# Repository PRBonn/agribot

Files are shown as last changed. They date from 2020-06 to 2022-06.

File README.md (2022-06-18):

## Update
1) remove tf dependencies and included tf2 similar to costmap2D and ros nav core packages. 
2) makes on Melodic and further

# AgriBot - Agricultural Mobile Robot Platform

---

### Youtube video

<div align="center">
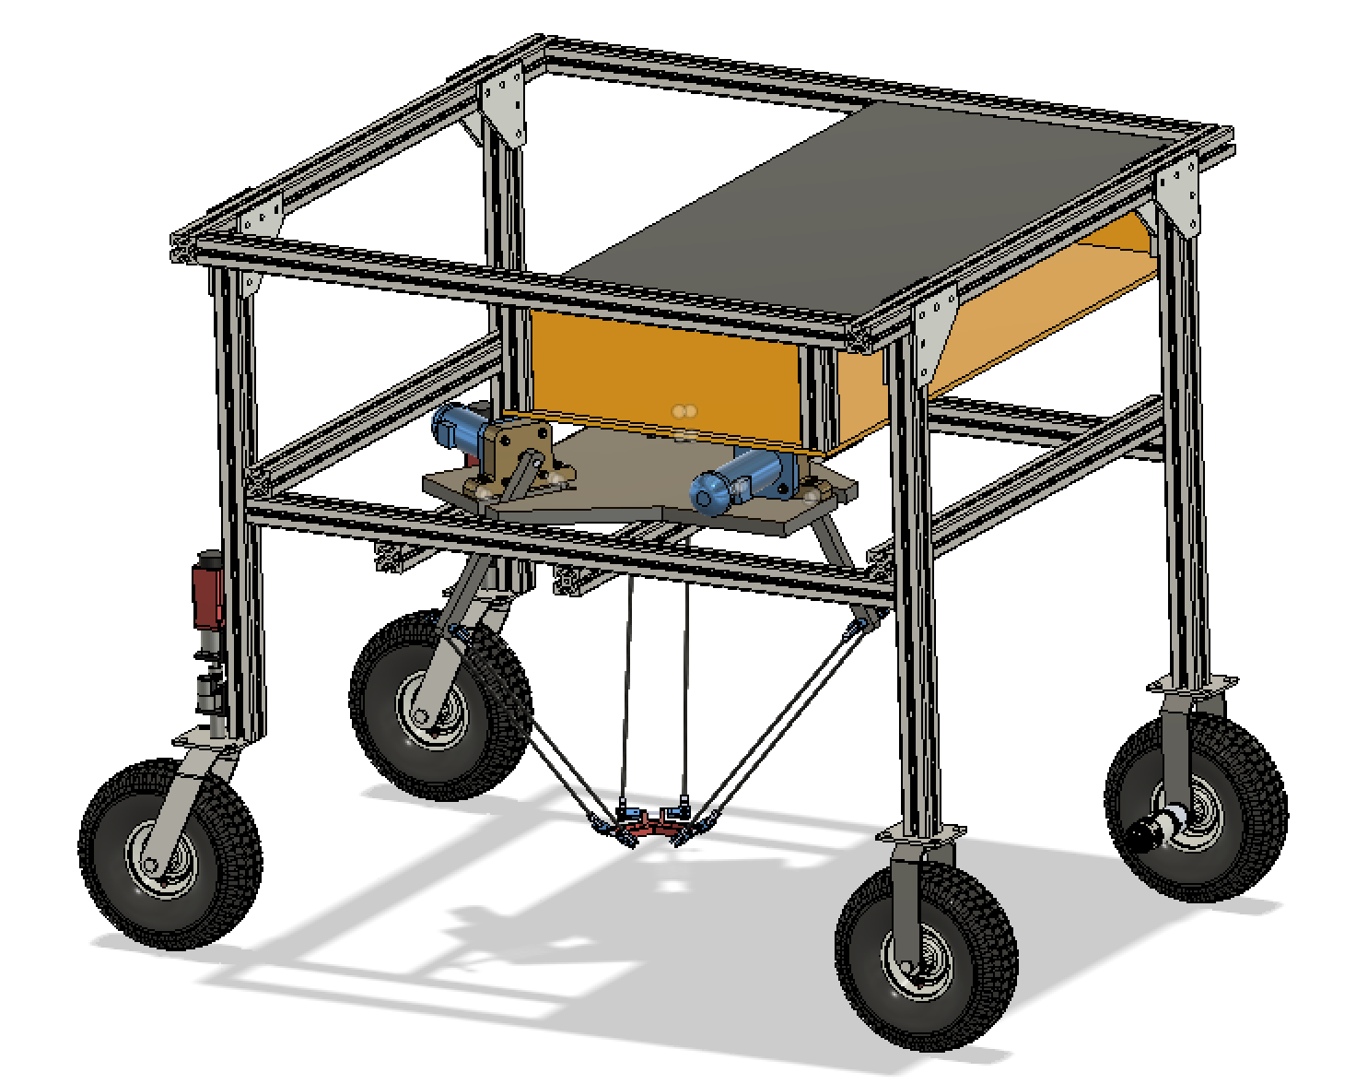
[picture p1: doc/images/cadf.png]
cadf
	
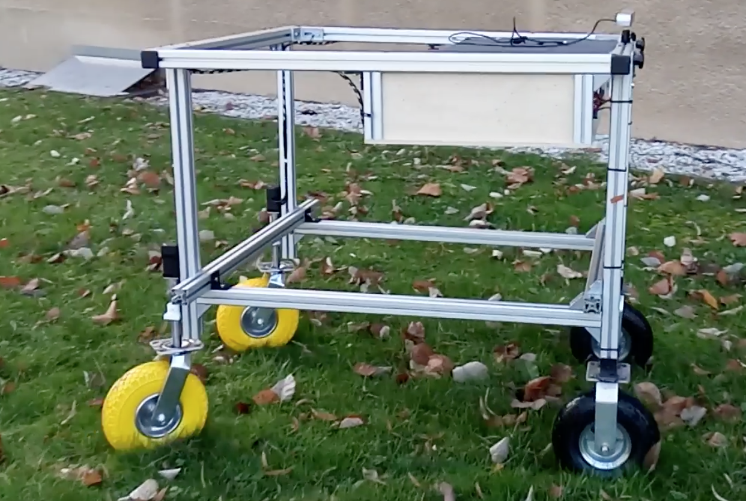
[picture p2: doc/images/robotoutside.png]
robotoutside
	
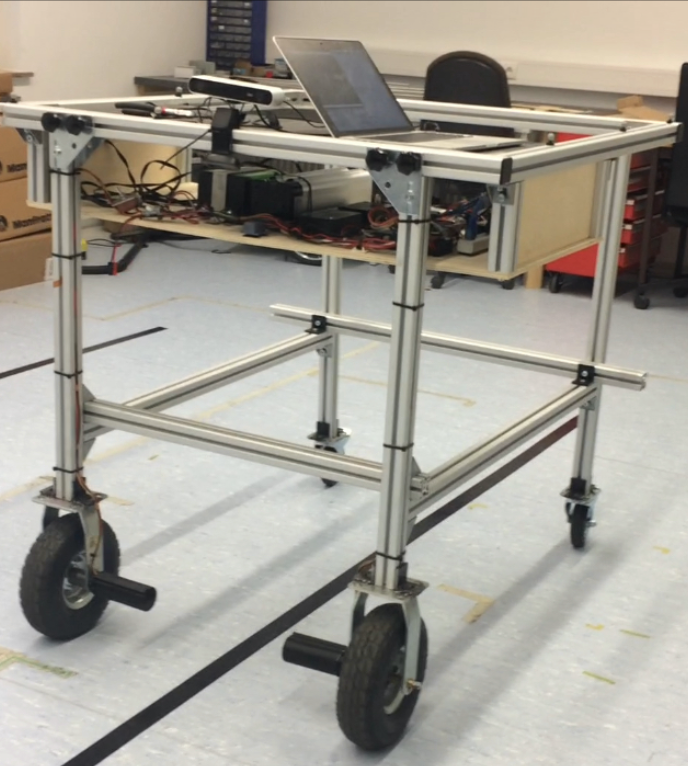
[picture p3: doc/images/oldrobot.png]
oldrobot
	
</div>

---
<div align="center">
	
YouTube Demo (https://youtu.be/aT82Srq7nwY?t=2)
	
</div>

## Project mission

The mission of the project is to build an agricultural robot (AgriBot) from
scratch with the aim of serving as a data-recording platform in fields.
For further information about the design and purpose of the robot, please follow the [About the AgriBot Project page](https://github.com/PRBonn/agribot/blob/master/doc/about.md)

---

## Getting Started
For easily bringing up the robot and recording data refer to [Easy bring up & Record Data](https://github.com/PRBonn/agribot/blob/master/doc/recorddata.md) which provides step-by-step
instructions to run the robot.

---

## Main Sections
- [Easy Bring up & Record Data :](https://github.com/PRBonn/agribot/blob/master/doc/recorddata.md)
  	Instructions for running the robot and recording the sensor data to a bagfile.
- [AgriBot Software :](https://github.com/PRBonn/agribot/blob/master/doc/api.md)
	Details about different packages written for the platform like navigation, localization, base controller, etc.
- [Mechanical Design :](https://github.com/PRBonn/agribot/blob/master/doc/mec.md)
	Detail about how mechanical structure has been designed and improved during the project time.
- [Electrical  Design :](https://github.com/PRBonn/agribot/blob/master/doc/elec.md)
	Electrical schematics and descriptions about connections and wiring protocols used in the robot.
- [Debug:](https://github.com/PRBonn/agribot/blob/master/doc/debug.md)
	Debug procedures for common problems.

---

<div align="center">
  


</div>

---

---
## Citation 
if you use this project in your recent works please reference to our paper by:

```bash

@article{ahmadi2021towards,
  title={Towards Autonomous Crop-Agnostic Visual Navigation in Arable Fields},
  author={Ahmadi, Alireza and Halstead, Michael and McCool, Chris},
  journal={arXiv preprint arXiv:2109.11936},
  year={2021}
}

@inproceedings{ahmadi2020visual,
  title={Visual servoing-based navigation for monitoring row-crop fields},
  author={Ahmadi, Alireza and Nardi, Lorenzo and Chebrolu, Nived and Stachniss, Cyrill},
  booktitle={2020 IEEE International Conference on Robotics and Automation (ICRA)},
  pages={4920--4926},
  year={2020},
  organization={IEEE}
}
```
---

## Maintenance
This repository is maintained by [Alireza Ahmadi](https://github.com/alirezaahmadi). In case of any problems, please don't hesitate to contact me.

 Alireza.Ahmadi@uni-bonn.de

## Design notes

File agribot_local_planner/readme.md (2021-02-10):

# AGRIBOT LOCAL PLANNER #

This package provide a simple implementation of a PID controller for robot
navigation. During robot navigation along a given path, this controller attempts
to stabilize both the linear and rotational velocity in an independent manner.
No velocity profile is computed before the robot starts moving. The environment
is considered static and, at the moment, no dynamics are taken into account.
This has been implemented as a ROS `move_base/base_local_planner` plugin.

## How to build ##

To build this package, just move it to your `catkin_ws` and build.

## How to run ##

The use of this package is constrained to the use of ROS `move_base` framework
for navigation. To use it as `base_local_planner`, add in your launcher in the
tag defining the `move_base` node the following line.
```
<param name="base_local_planner" value="agribot_local_planner/AgribotLocalPlanner" />
```
A simple tuning of the PID controller is provided. However, it may need to be
newly tuned accordingly to the robot and task taken into account. To this end,
controller parameters have been defined as dynamic parameters and can be tuned
using `dynamic_reconfigure`.

Enjoy!

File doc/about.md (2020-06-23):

# AgriBot - A New Agricultural Mobile Robot Platform

---

## About The Project
The aim of the project is to develop a robot to perform basic localization and navigation tasks in agricultural applications. More precisely, the robot should embody a platform that is able to navigate autonomously in the fields and offers enough room for the assembly of task specific actuators like herbicide nozzles or additional sensors like cameras.
To achieve this goal, three main tasks have to be solved: the hardware design, the localization and the navigation. The first stage of development is the mechanical design of the robot. Requirements for the design are, that the platform is lightweight and easy to transport while being big enough to pass over crop rows and having space for the mentioned additional equipment. On top of the design of the layout of the platform, the sensors and actuators used for localization and navigation have to be decided on. The result of this first stage is a platform that can drive while being steered by a joystick controller.
The second step during the development is the localization of the robot. To be able to navigate autonomously it is essential that the robot pose relative to the field is known. Task of the localization is to use the given sensor data and give an estimation of this pose that is precise enough for the last step, the navigation.
During the navigation, the pose estimate of the localization in combination with a map of the field is taken as input and the necessary motion commands to follow a given trajectory through the field are returned. Consequently, at this point in time the joystick controller is not needed any more, as the motion commands are generated by the navigation module and the robot drives autonomously.

<!-- <div align="center">
	<img src="/doc/images/mechanic.png" alt="mechanic" width="600" title="mechanic"/>
</div> -->

---

*Note that* this repository is maintaining by [Alireza Ahamdi](https://github.com/PRBonn). 
In case of facing any problem don't hesitate to constant me.

---
[The Main ReadMe](https://github.com/PRBonn/agribot/blob/master/README.md)

*Section* 
- [Mechanical Design](https://github.com/PRBonn/agribot/blob/master/doc/mec.md)
- [Electrical  Design](https://github.com/PRBonn/agribot/blob/master/doc/elec.md)
- [AgriBot Software](https://github.com/PRBonn/agribot/blob/master/doc/api.md) 
- [Record Data](https://github.com/PRBonn/agribot/blob/master/doc/recorddata.md) 
- [Debug](https://github.com/PRBonn/agribot/blob/master/doc/debug.md)

--- 
  by: [Alireza Ahmadi](https://github.com/alirezaahmadi)                                     
 University of Bonn- Robotics & Geodetic Engineering

 Alireza.Ahmadi@uni-bonn.de

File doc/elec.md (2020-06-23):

# AgriBot - A New Agricultural Mobile Robot Platform

---

**`WARNING`** please attention to warnings:
- In case of having some pins disconnected or broken, please first read the tutorials to debug the problem and **'do not try your luck, otherwise, definitely you will burn some part!!!'**, or you can contact with [Alireza Ahmadi](https://github.com/PRBonn) as the designer of the robot.
- In case of noticing any delay in responds from the robot, please restart the nodes and connections.
- Always check the main connections (power, USB cables, Joystick) before turning the robot 'ON'.

---

## Table of Contents
- [Electrical Design](https://github.com/PRBonn/agribot/blob/master/doc/elec.md#electrical-design)
  - [Power UP the AgriBot](https://github.com/PRBonn/agribot/blob/master/doc/elec.md#power-up-the-agribot)
  	- [Logic level Battery](https://github.com/PRBonn/agribot/blob/master/doc/elec.md#logic-level-battery)
  	- [High level Battery](https://github.com/PRBonn/agribot/blob/master/doc/elec.md#high-level-battery)
    - [How to Charge the Agribot](https://github.com/PRBonn/agribot/blob/master/doc/elec.md#how-to-charge-the-agribot)
  - [Power Management Part](https://github.com/PRBonn/agribot/blob/master/doc/elec.md#power-management-part)
  - [Serial Communication, I/O Pins](https://github.com/PRBonn/agribot/blob/master/doc/elec.md#serial-communication-io-pins)
  	- [IMU node Connection](https://github.com/PRBonn/agribot/blob/master/doc/elec.md#imu-connection)
  	- [RearServo's Connections](https://github.com/PRBonn/agribot/blob/master/doc/elec.md#rearservos-connections)
  	- [Front Actuators Connections](https://github.com/PRBonn/agribot/blob/master/doc/elec.md#front-actuators)
  - [Reset Relays](https://github.com/PRBonn/agribot/blob/master/doc/elec.md#reset-relays)
  - [Alarm](https://github.com/PRBonn/agribot/blob/master/doc/elec.md#alarms)

---

## Electrical Design

Electrical section of the AgriBot includes controlling layers, sensors, battery management system (BMS) and actuators. The control layers’ structure is shown in below which is comprised of two different major layers, Low-level controllers and User layer which are containing DCM (Device Communication Manager), Sensors and User layers. The main program executed on Low-level controller runs on a Raspberry Pi 3 embedded controller and directly controls all the sensors and actuators, also runs master of ROS to manage all nodes working in the network. This layer is responsible for time synchronization of whole connections and I/O’s used in the process, like reading the IMU (Inertial Measurement Unit) and controlling all four actuators for driving and steering the robot. 

<div align="center">
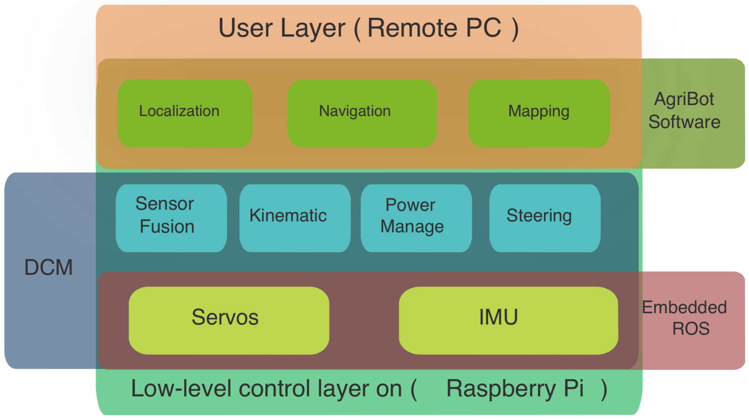
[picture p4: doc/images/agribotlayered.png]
agribotlayered
  
</div>

Also, it runs the main nodes which drive the robot based on defined kinematics and provides a basic fusion of the sensors for localization out of IMU, wheel odometry and GPS. This layer of control is accessible via [SSH](https://www.hostinger.com/tutorials/ssh-tutorial-how-does-ssh-work#gref). This type of connection makes user able to connect and stream out the status of all sensors and to implement his own high-level algorithms though establishing a client node to ROS master which mainly is running on Raspberry Pi.

<div align="center">
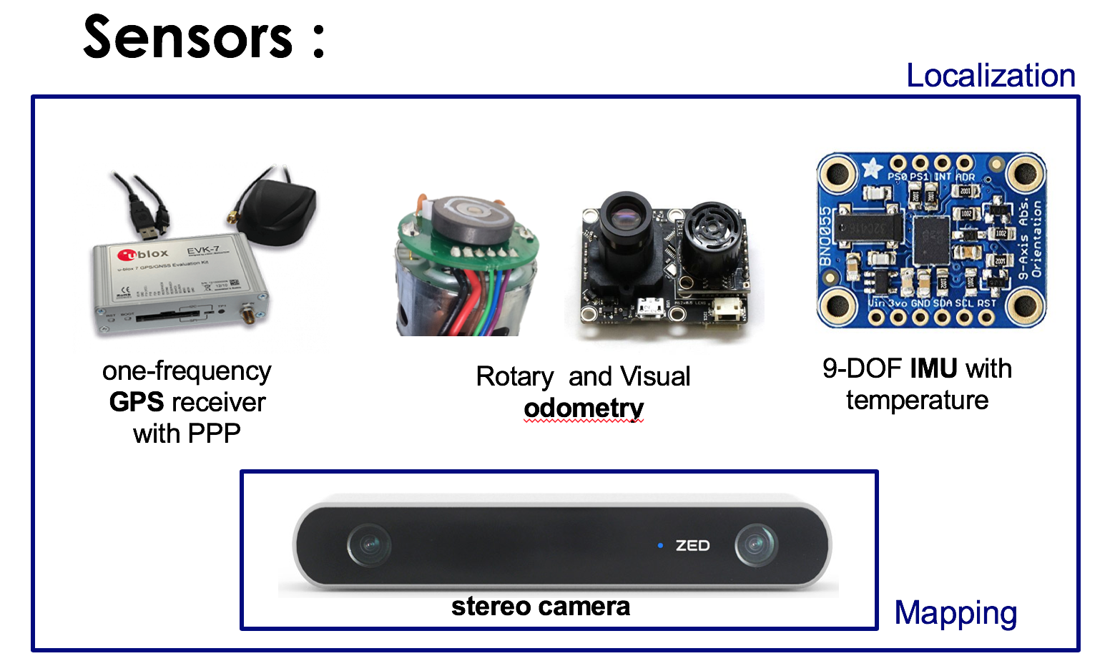
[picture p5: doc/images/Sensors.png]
Sensors
  
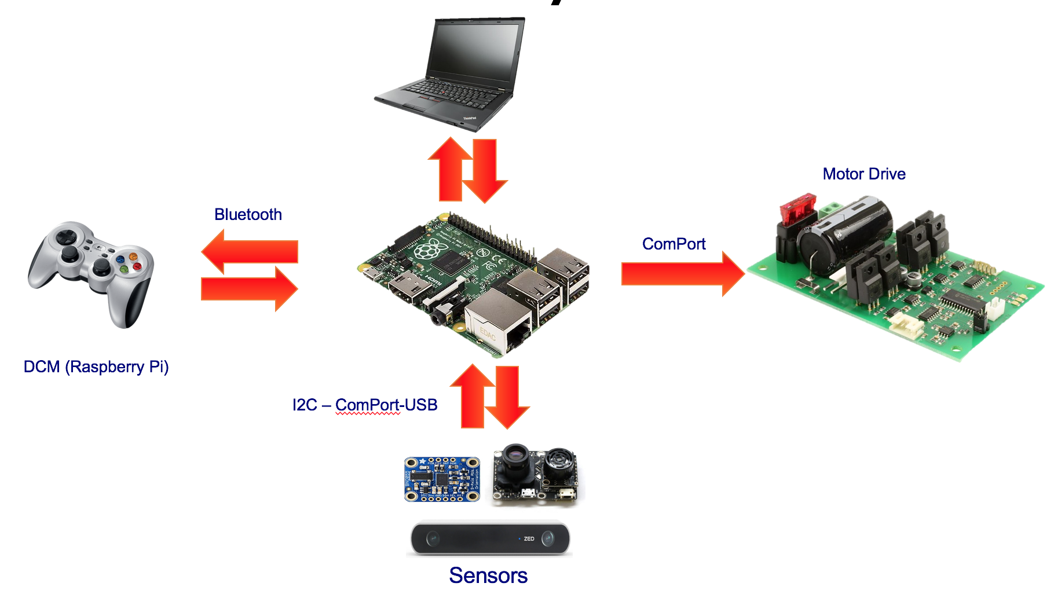
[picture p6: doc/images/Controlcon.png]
Controlcon
  
</div> 

---

## Power UP the AgriBot
The designed robot uses two batteries to power up all the actuators and electrical equipments. 
To turn on the robot, simply change the states of two switches in front of the robot (in the box) to *NO*. The images in below show the switches which control the power.

<div align="center">
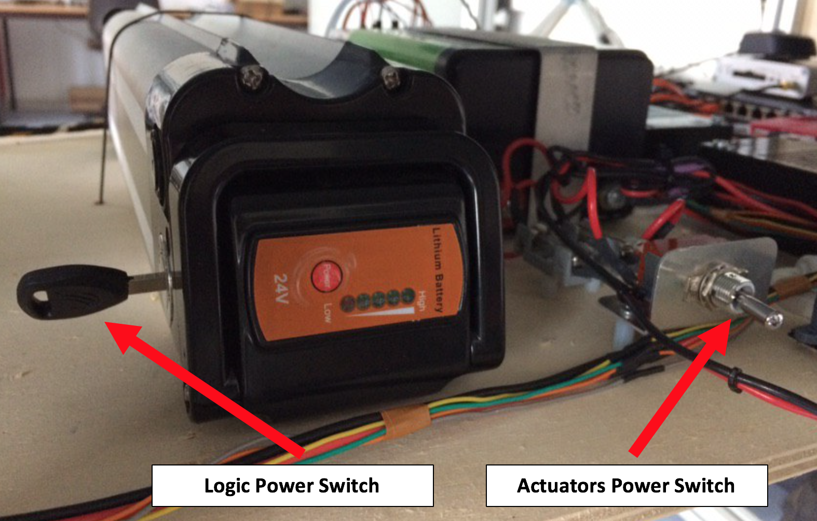
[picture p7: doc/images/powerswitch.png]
powerswitch battery switches
  
</div>

### Logic level Battery
It's used to power up all the equipments working with logic level of voltage (3.3v ~ 5v). including Raspberry PI, Arduino controllers, Ethernet switch, USB hub and etc.

<div align="center">
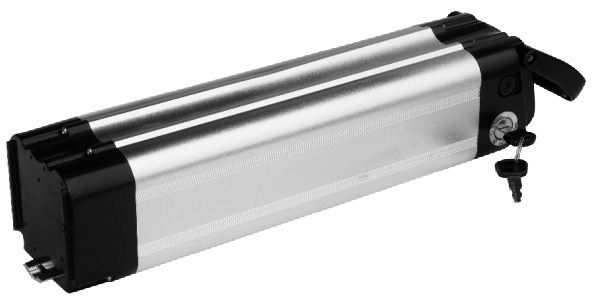
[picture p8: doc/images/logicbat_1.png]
logicbat_1 Logic power battery switch
	
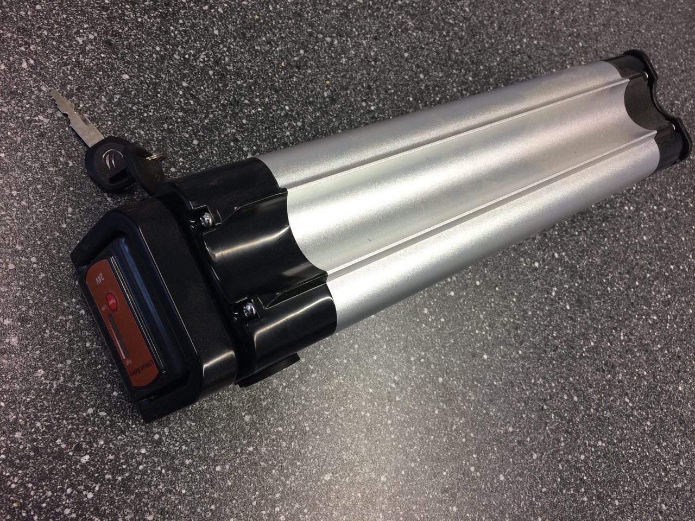
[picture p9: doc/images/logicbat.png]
logicbat Logic power battery
	
</div> 

### High level Battery
This battery is specially used to supply actuators and their drivers.

<div align="center">
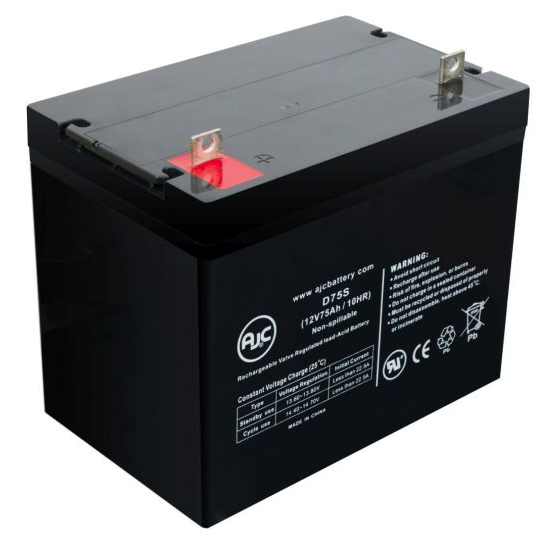
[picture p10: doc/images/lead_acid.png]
lead_acid lead acid battery
	
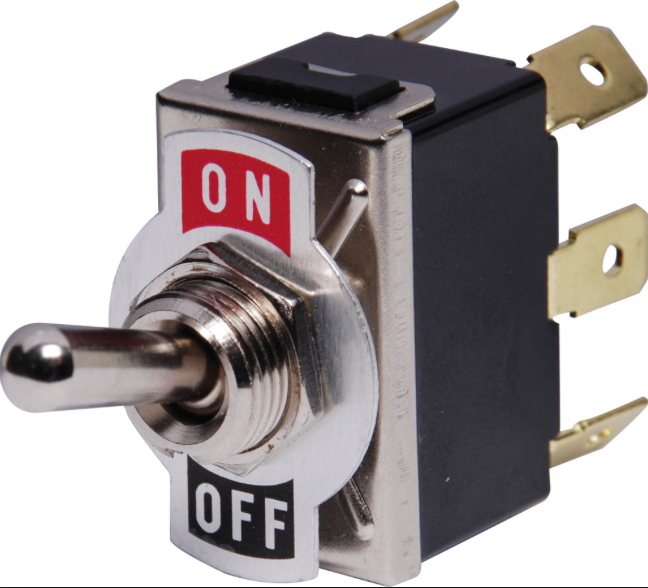
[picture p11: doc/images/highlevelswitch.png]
highlevelswitch High level switch
	
</div>

### How to Charge the Agribot
As robot has two different batteries, it uses two different chargers with sockets shown in image below to charge.

<div align="center">
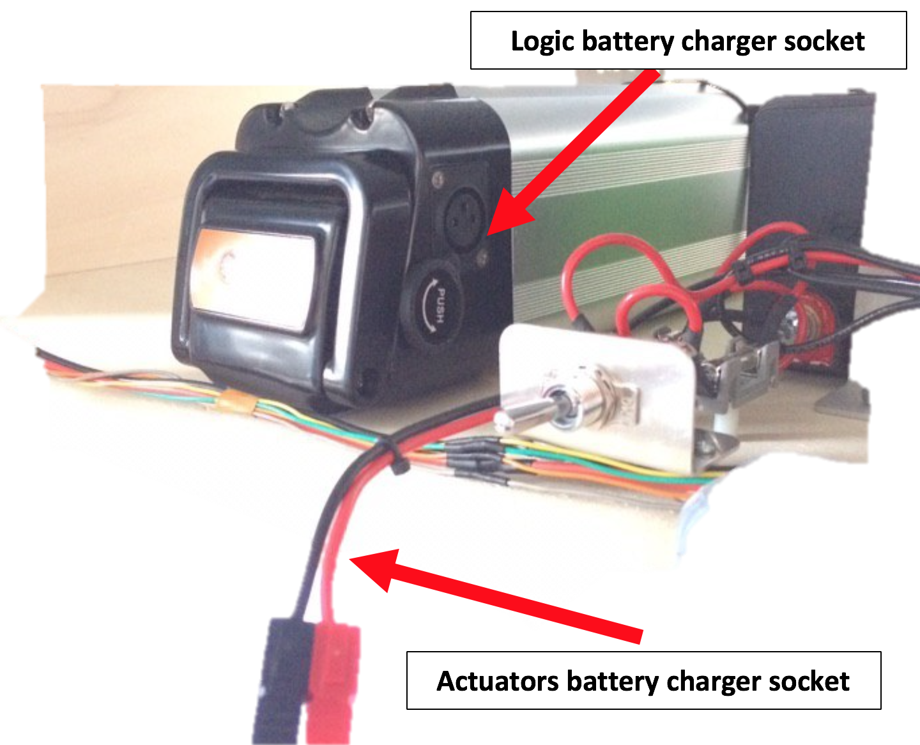
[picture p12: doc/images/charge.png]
powercharge battery charger sockets
  
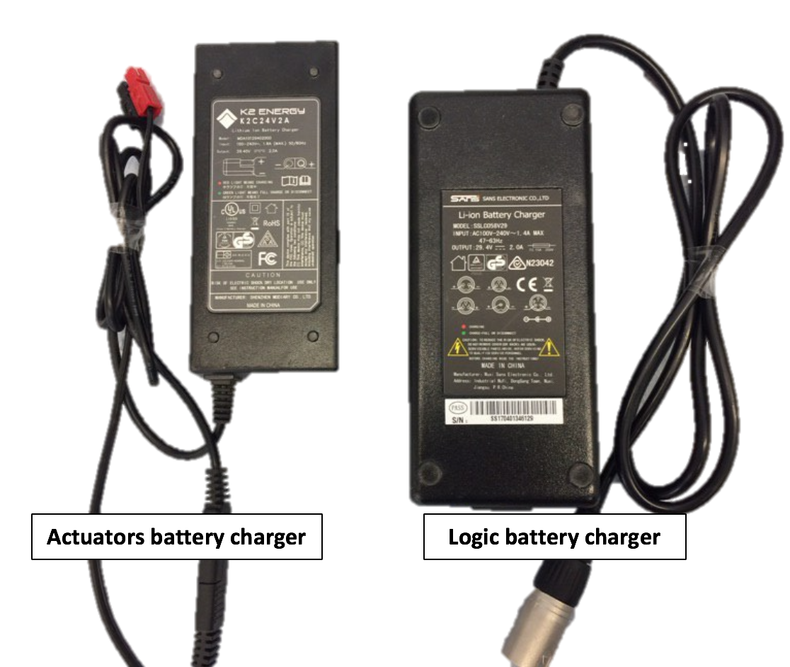
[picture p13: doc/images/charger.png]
powercharge battery charger
  
</div>  

*`NOTE`* both chargers have a LED to show the status of charge. 
* *RED* is charging...
* *GREEN* is full...

### HOW to Turn-Off the robot

to shutdown the robot first run the command below, to shutdown the raspberry pi and then swtich of both power keys shown in [here](https://github.com/PRBonn/Agribot/raw/master/doc/images/powerswitch.png)

```
sudo poweroff
```

---

## Power Management Part
In such heavy and equipped robot, which needs to operate for a long time in uneven and/or muddy fields with lots of sensors and actuators which should be supplied properly, the power supply gets really important, in such a way that, if one of the controllers or sensors can’t get sufficient amount of power, it will cause unexpected neglects in operation which can directly affect how precise the tasks are achieved by the robot. Hence, the AgriBot uses two separate rechargeable 24v batteries to power up electrical tools. All the actuators are supplied through a 24v/5A battery which isolates the electrical connection of drive part from digital and sensor parts which use other 24v/10A battery to run. This separation avoids from effecting noses arisen from motors and drivers on main processor and logic parts. Also, each logic device gets its power from a separate regulator channel and this guarantees to have a stable working period for all electrical stuff. 

Power distribution task is done by using a regulator board which provides different voltages. Regulator board has two input sockets and ten outputs which each output unit provides four different levels of voltages: 0v (GNG), 5v, 12v, 24v. In image below the configuration of input and output pins are marked.

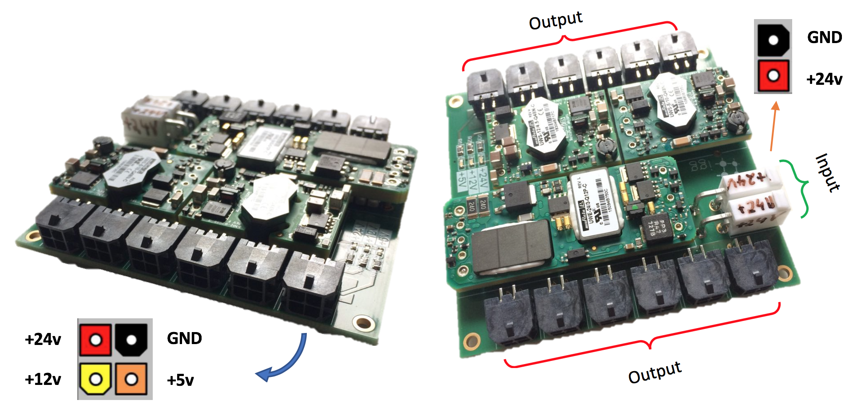
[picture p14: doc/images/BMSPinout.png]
BMSPinout


as its show in image below: all  supplied devices through BMS board are getting their power from bike-battery(with aluminum body).

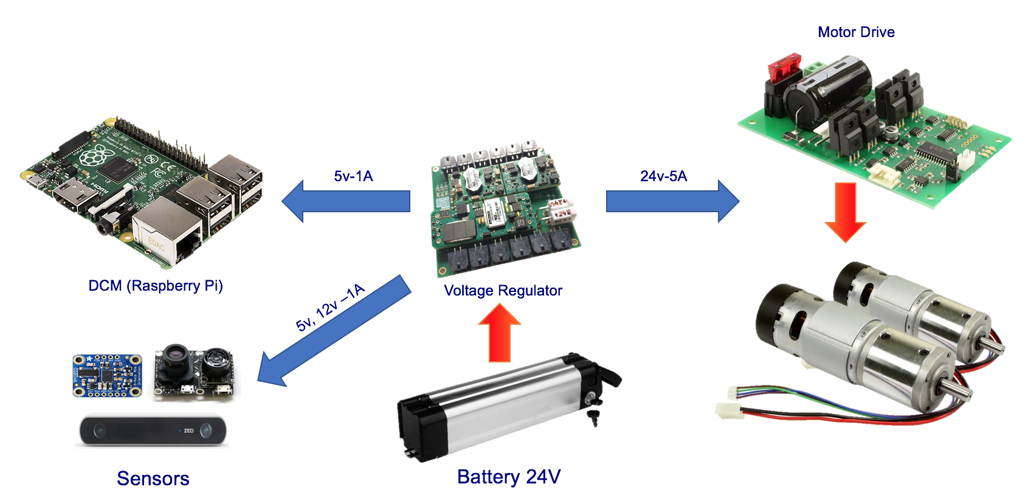
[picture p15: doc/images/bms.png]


hence, all actuators are driven by other battery to isolate the logic level equipments from power section (to avoid getting disturbed by actuators produced noise).

---

## Serial Communication, I/O Pins
Some equipments like IMU, Drivers and Reset relays are connected to reaspberry pi by I/O pins and serial to USB converters. connection map is shown in image below.

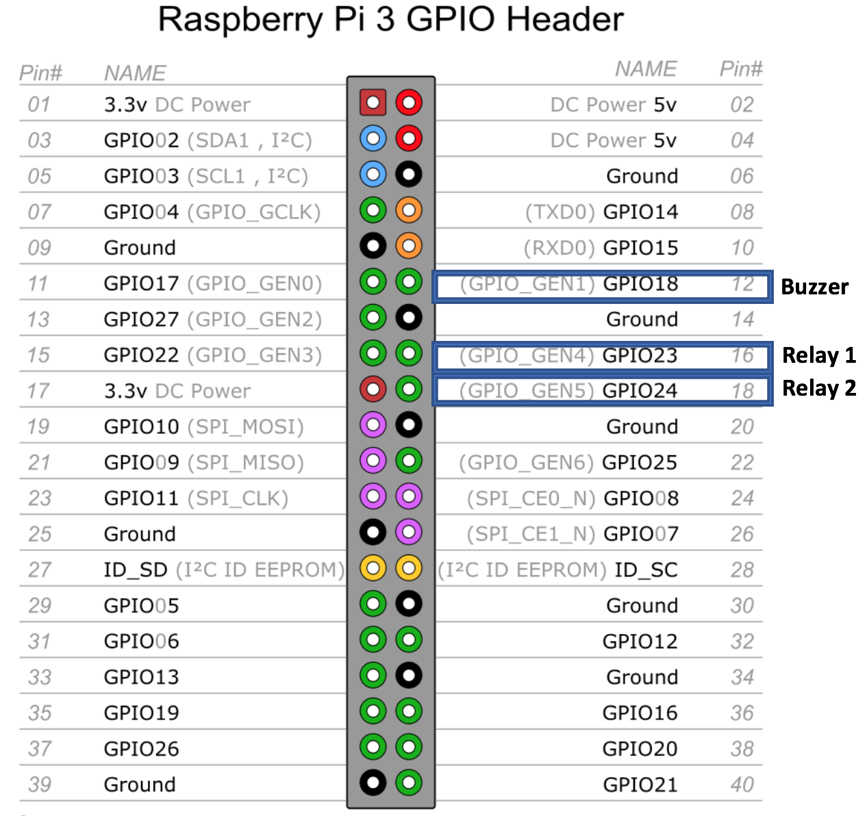
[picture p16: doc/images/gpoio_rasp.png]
raspberrypigpio raspberry


### IMU Connection
IMU node as its completely explained in [agribot_imu](https://github.com/PRBonn/agribot/blob/master/doc/api/agribot_imu.md) section is an Embedded-ROS node which uses an *Arduino-ProMicro* board to read the sensor and publish the topic */imu* in network. its connection is shown in image below:

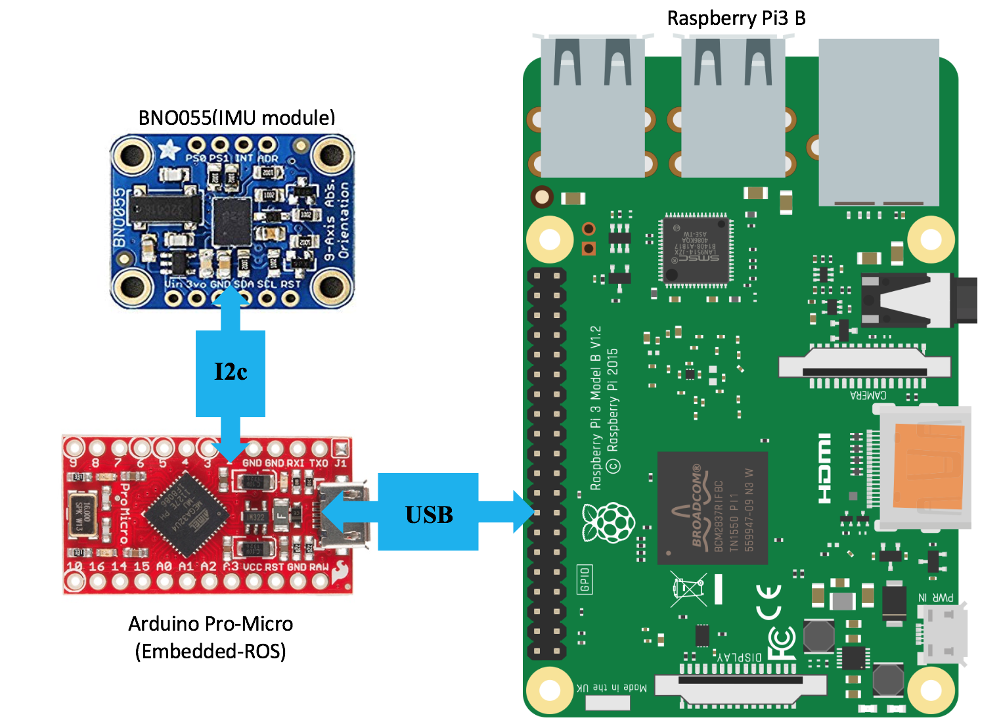
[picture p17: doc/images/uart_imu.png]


### RearServo's Connections
Rear caster wheels are motorized, by adding a perpendicular joint to their main axis, therefore their rotation around the Z-axis can be controlled by motion controller node. Also, this capability is implemented through an Embedded-ROS node running on a *Arduino-UNO* board. 

<div align="center">
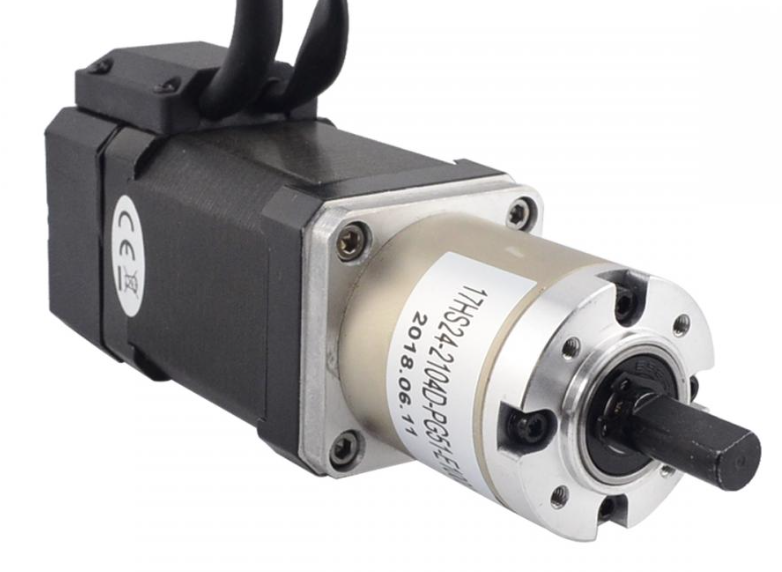
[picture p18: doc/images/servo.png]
servo
  
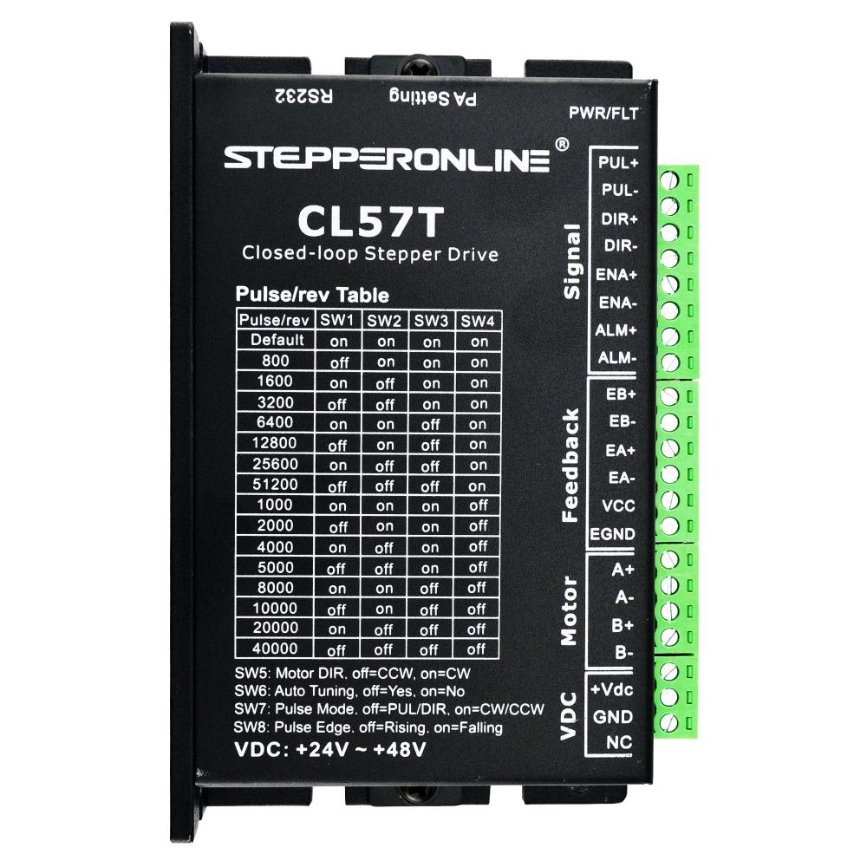
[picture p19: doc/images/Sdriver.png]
Sdriver
  
</div>

* [Stepper motor](https://www.omc-stepperonline.com/closed-loop-stepper-motor/Nema-17-Closed-loop-Geared-Stepper-L60mm-Gear-Raio-511-Encoder-1000CPR.html)
* [Closed loop stepper driver](https://www.omc-stepperonline.com/closed-loop-stepper-driver/closed-loop-stepper-driver-0-70a-24-48vdc-for-nema-17-23-24-stepper-motor-cl57t.html)

The image below shows all connections related to rear-servos. 

<div align="center">
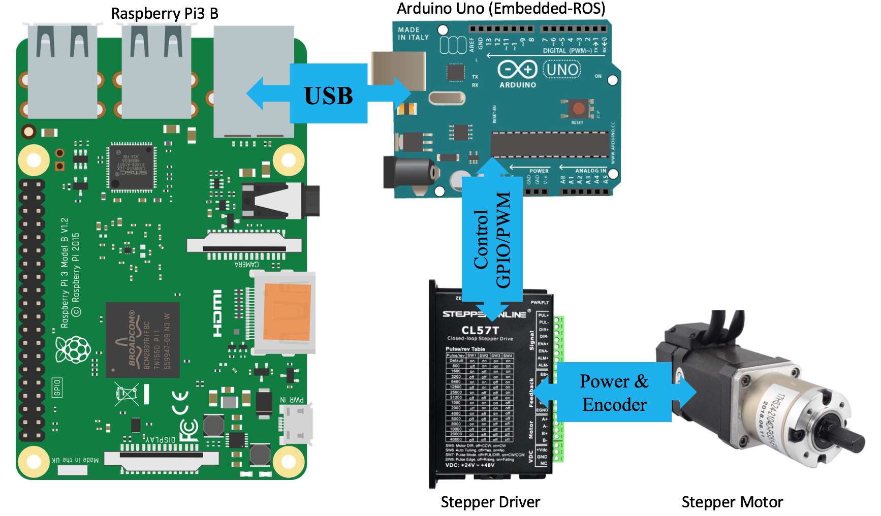
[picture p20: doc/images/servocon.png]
servocon
  
</div>

To find out more about the controller node please visit [agribot_servo](https://github.com/PRBonn/agribot/blob/master/doc/api/agribot_servo.md) package, which tries to explain all the details about connections and controller node.

--- 

### Front Actuators

AgriBot platform is equipped  with two geared DC-motors which, are connected to the Raspberry Pi (Local processor on AgriBot) via USB (Virtual Com-Port). Image below shows the driver and actuator model with related links.

<div align="center">
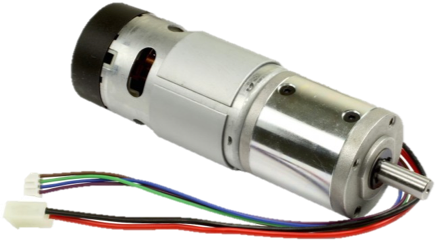
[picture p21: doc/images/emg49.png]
EMG49
  
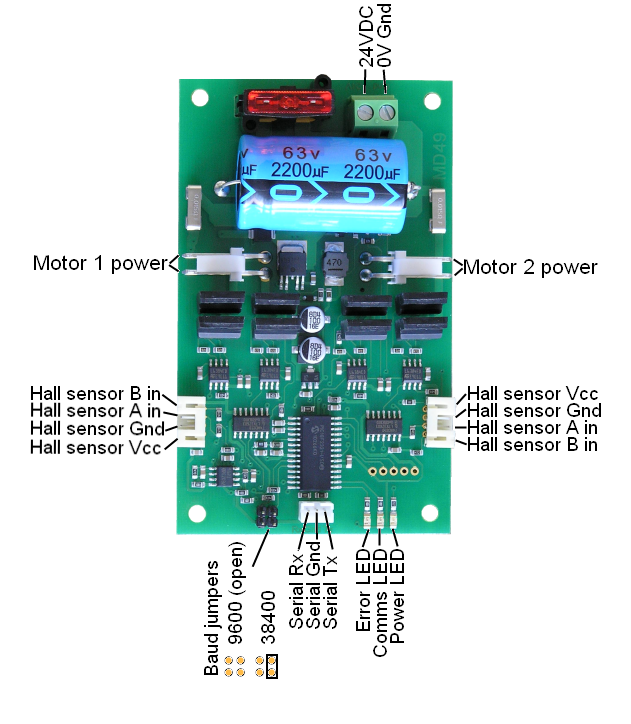
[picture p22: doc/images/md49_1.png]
MD49
  
</div>

* [Driving motors - EMG49](https://robot-electronics.co.uk/products/drive-systems/emg49-gearmotor-with-encoder.html)
* [front wheel's Driver - MD49](https://robot-electronics.co.uk/md49-24v-5a-dual-h-bridge-motor-driver.html)

The image below shows all connections related to front actuators. 

<div align="center">
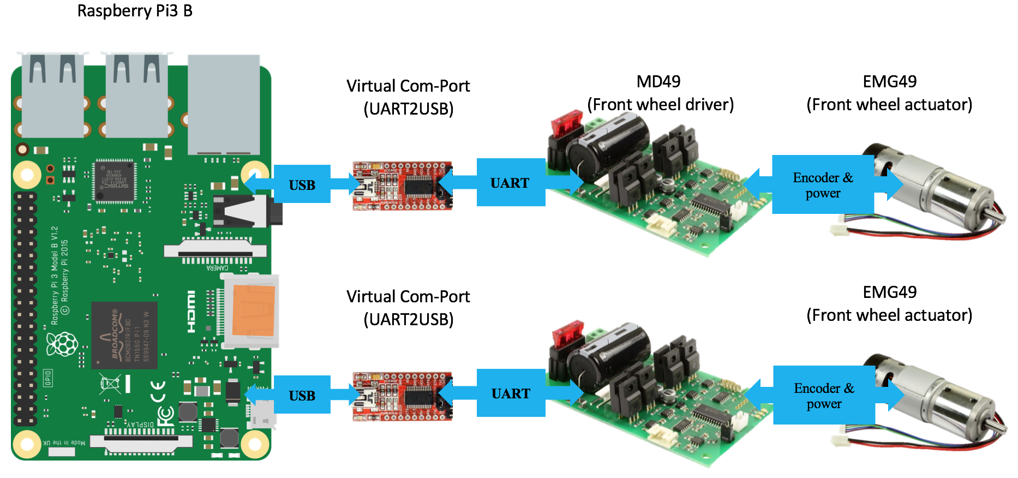
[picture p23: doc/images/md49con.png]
md49con
  
</div>

To find out more about the controller node please visit [agribot_base_controller](https://github.com/PRBonn/agribot/blob/master/doc/api/agribot_base_controller.md) package, which tries to explain all the details about connections and controller node.

---

## Reset Relays
As its explained in [agribot_base_controller](https://github.com/PRBonn/agribot/blob/master/doc/api/agribot_base_controller.md) in case of occurring any problem in serial communication with actuators (front/back) two relays are utilized to automatically reset the power of drivers and re-establish the connections. this part which contains a relay board is shown in image below:

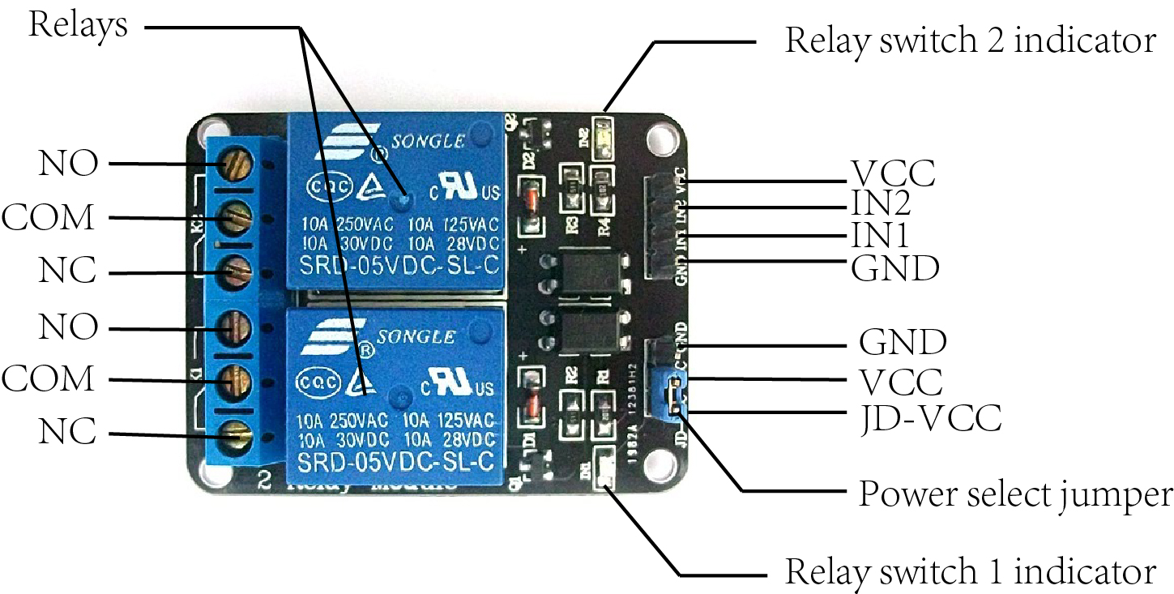
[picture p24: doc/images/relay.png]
relay


## Alarms

Also, a buzzer is used to warn the low battery or any other electrical/software faults through some alarms:
the module is shown in below:

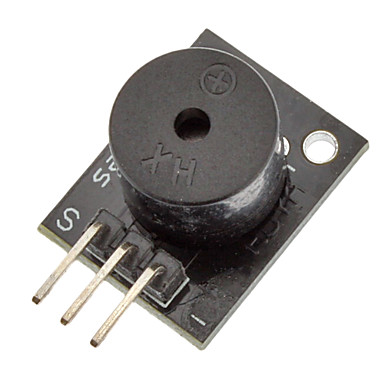
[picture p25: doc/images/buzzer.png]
buzzer


The Alarm code is shown in table below:

| Type of Alarm  | Repeat-Number | Repeat-Duration(ms) | Error/Notification | How to fix | 
| --- | --- | --- | --- | --- |
| Broken | 2 | 300  | Base launched | --- |
| Continues | -- | -- | Low Battery | [Debug The Power Status](https://github.com/PRBonn/agribot/blob/master/doc/debug.md#debug-the-power-status) |
| Broken | 5 | 70  | Serial Communication Error | [Debug The Electrical Connections](https://github.com/PRBonn/agribot/blob/master/doc/debug.md#debug-the-electrical-connections)

Also, a simple log of the error will be printed on the terminal which base is launched.

**`NOTE`** all the connections used to control these part via raspberry pi is illustrated in [Raspberry Pi GPIOs](https://github.com/PRBonn/Agribot/raw/master/doc/images/gpoio_rasp.png)

---
[The Main ReadMe](https://github.com/PRBonn/agribot/blob/master/README.md)

*Section* 
- [Mechanical Design](https://github.com/PRBonn/agribot/blob/master/doc/mec.md)
- [AgriBot Software](https://github.com/PRBonn/agribot/blob/master/doc/api.md) 
- [Easy Bring up & Record Data](https://github.com/PRBonn/agribot/blob/master/doc/recorddata.md) 
- [Debug](https://github.com/PRBonn/agribot/blob/master/doc/debug.md)

--- 
 by: [Alireza Ahmadi](https://github.com/alirezaahmadi)                                     
 University of Bonn- Robotics & Geodetic Engineering

 Alireza.Ahmadi@uni-bonn.de

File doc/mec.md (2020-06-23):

# AgriBot - A New Agricultural Mobile Robot Platform

---

## Table of Contents
- [Mechincal Design](https://github.com/PRBonn/agribot/blob/master/doc/mec.md#mechincal-design)
  - [AgriBot CAD Model](https://github.com/PRBonn/agribot/blob/master/doc/mec.md#agribot-cad-model)
  - [AgriBot Body Dimensions](https://github.com/PRBonn/agribot/blob/master/doc/mec.md#agribot-body-dimensions)
---

## Mechincal Design
The designed platform aims to work on the agricultural field to collect data and does weed control operations. The mentioned scope of activities requires special specifications in the electrical and mechanical parts of the robot. The robots mechanical structure should be rigid enough to conserve all equipment undamaged in uneven grounds and adverse weather conditions. 

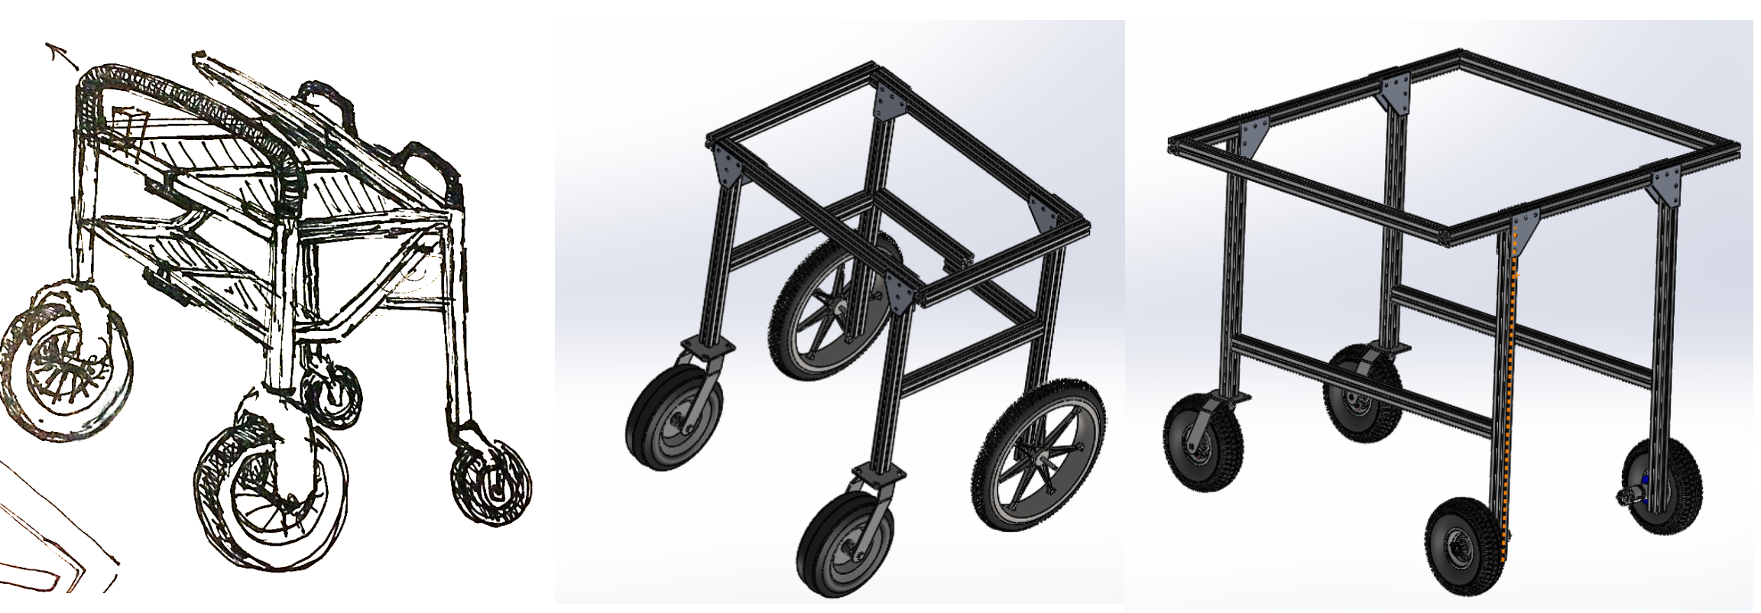
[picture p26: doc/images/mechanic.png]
mechanic


--- 

### AgriBot CAD Model
Primary sketches and models have done in Solidworks simulation software and then developments are applied in Fusion 360 from AutoCAD. The final model is shown here.

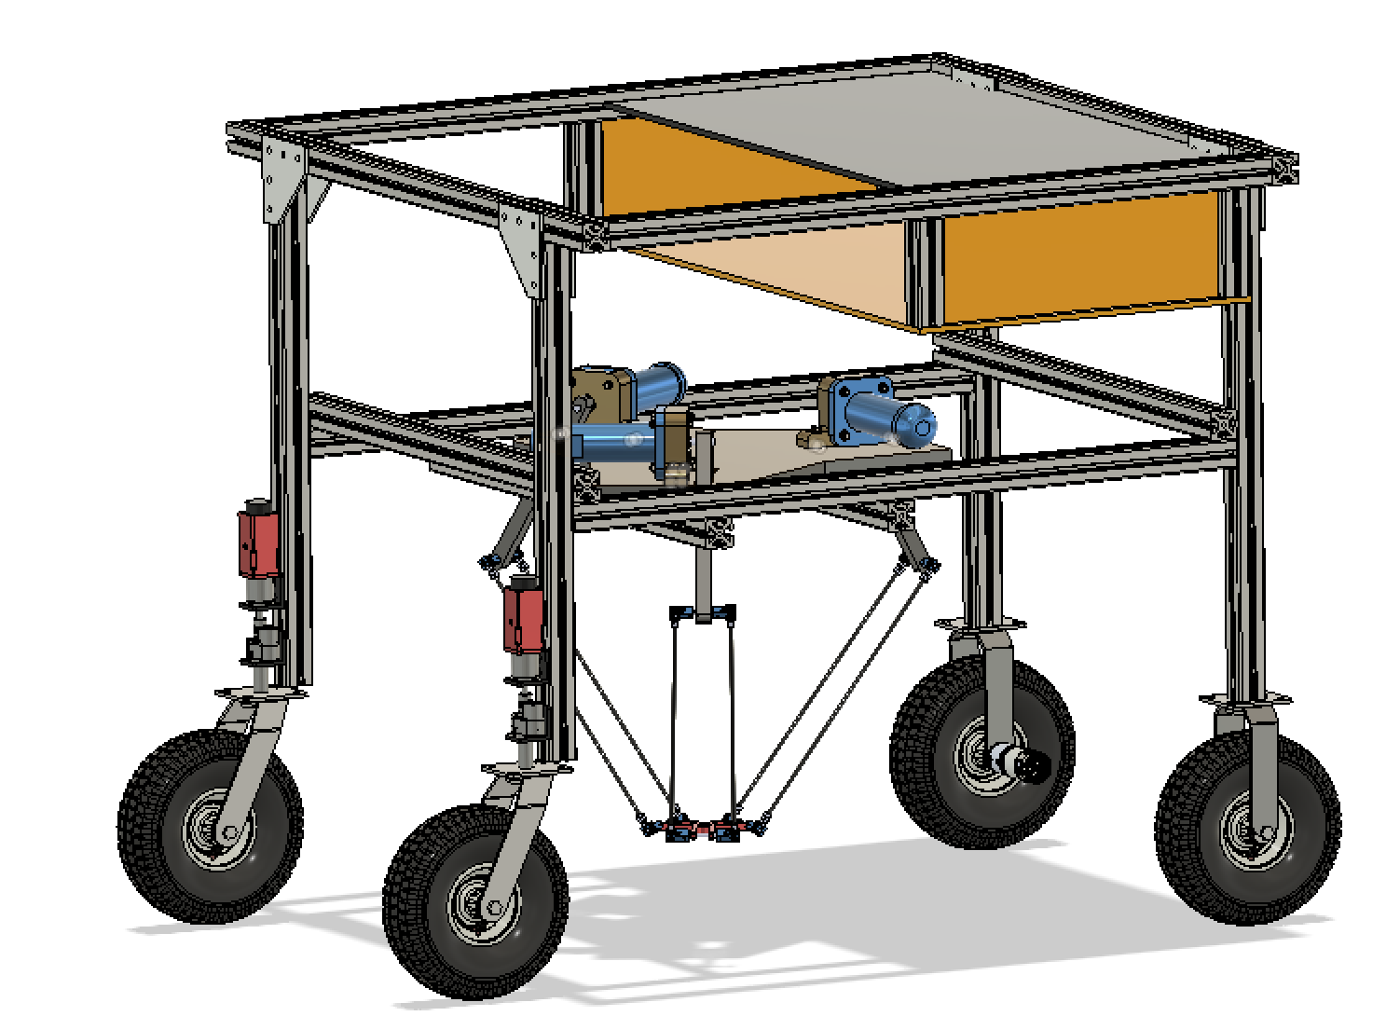
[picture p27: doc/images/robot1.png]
fusion360


*Reference* 

Delta ARM robot CAD model take from GrabCad-[halit şahin](https://grabcad.com/library/delta-robot-8)

---

### AgriBot Body Dimensions
AgriBots body has designed upon a basic idea to be rigid enough and flexible to be easily transportable. hence, it has a square shaped top section and two legs with 1052mm in height which each leg holds two wheels in the front and the back. 

<div align="center">ds Dimensions</div>

* Radius of wheels: 150mm
* Height: 1052mm
* Width: 1000mm
* Length: 1080 (or 1170mm in center-to-center of wheels)
* Wright: about 35kg

---
[The Main ReadMe](https://github.com/PRBonn/agribot/blob/master/README.md)

*Section* 
- [Electrical  Design](https://github.com/PRBonn/agribot/blob/master/doc/elec.md)
- [AgriBot Software](https://github.com/PRBonn/agribot/blob/master/doc/api.md) 
- [Easy Bring up & Record Data](https://github.com/PRBonn/agribot/blob/master/doc/recorddata.md) 
- [Debug](https://github.com/PRBonn/agribot/blob/master/doc/debug.md)

---

all files can be found on shared project in AutoCAD cloud repository. in case of any question please contact [Alireza Ahmadi](https://github.com/PRBonn)

--- 
 by: [Alireza Ahmadi](https://github.com/alirezaahmadi)                                     
 University of Bonn- Robotics & Geodetic Engineering

 Alireza.Ahmadi@uni-bonn.de

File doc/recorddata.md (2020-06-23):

# AgriBot - A New Agricultural Mobile Robot Platform

---

## Table of Contents
- [How to Power up the AgriBot](https://github.com/PRBonn/agribot/blob/master/doc/recorddata.md#how-to-power-up-the-agribot)
   - [How to Charge the Agribot](https://github.com/PRBonn/agribot/blob/master/doc/recorddata.md#how-to-charge-the-agribot)
- [How to Connect to AgriBot](https://github.com/PRBonn/agribot/blob/master/doc/recorddata.md#how-to-connect-to-agribot)
  - [PC Setup](https://github.com/PRBonn/agribot/blob/master/doc/recorddata.md#pc-setup)
  	- [Wifi Connection](https://github.com/PRBonn/agribot/blob/master/doc/recorddata.md#wifi-connection)
  	- [Ethernet Connection](https://github.com/PRBonn/agribot/blob/master/doc/recorddata.md#ethernet-connection)
  - [Bring up](https://github.com/PRBonn/agribot/blob/master/doc/recorddata.md#bring-up)
  	- [Log into AgriBot PC using HDMI display](https://github.com/PRBonn/agribot/blob/master/doc/recorddata.md#log-into-agribot-pc-using-hdmi-display)
  	- [Log into AgriBot PC using SSH connection](https://github.com/PRBonn/agribot/blob/master/doc/recorddata.md#log-into-agribot-pc-using-ssh-connection)
  	- [Using Screen Tool](https://github.com/PRBonn/agribot/blob/master/doc/recorddata.md#using-screen-tool)
  	- [Run the roscore](https://github.com/PRBonn/agribot/blob/master/doc/recorddata.md#run-the-roscore)
  	- [Run the Base Controller of AgriBot](https://github.com/PRBonn/agribot/blob/master/doc/recorddata.md#run-the-base-controller-of-agribot)
- [How to Use JoyStick](https://github.com/PRBonn/agribot/blob/master/doc/recorddata.md#how-to-use-joystick)
- [Easy Bring up for AgriBot](https://github.com/PRBonn/agribot/blob/master/doc/recorddata.md#easy-bring-up-for-agribot)
- [Record Data](https://github.com/PRBonn/agribot/blob/master/doc/recorddata.md#how-to-record-data)
- [How to Turn-Off the robot](https://github.com/PRBonn/agribot/blob/master/doc/recorddata.md#how-to-turn-off-the-robot)

---

## How to Power up the AgriBot
The AgriBot uses two batteries. One battery is used to power up all the
actuators (front and back wheel motor). The second battery is used to supply
power to all the electrical equipments including the on-board raspberry- pi
and other sensors. To turn on the robot, simply change the states of two
switches in front of the robot (in the box) to *ON*. The image below shows the
switches to turn on the power.

<div align="center">
	powerswitch battery switches
</div> 

### How to Charge the AgriBot
As robot has two different batteries, it uses two different chargers with sockets shown in image below to charge.

<div align="center">
	powercharge battery charger sockets
  powercharge battery charger
</div> 

You can find more information about the electrical design and connections in
[Electrical
Design](https://github.com/PRBonn/agribot/blob/master/doc/elec.md)

---

## How to Connect to AgriBot

These instructions are to guide the user to properly make the connection
between a remote PC (your PC) and the AgriBot on-board PC. You can connect to
the AgriBot using either Wifi or Ethernet using ROS platform and
[SSH](https://www.hostinger.com/tutorials/ssh-tutorial-how-does-ssh-work#gref)
connection.

### Remote PC setup

Preparing the Remote PC (your laptop) to communicate with the AgriBot.

#### Install Ubuntu and ROS on your PC
- to install Ubuntu you can use following instructions on suggested website [How to install Ubuntu](https://tutorials.ubuntu.com/tutorial/tutorial-install-ubuntu-desktop#0)
- to install ROS use [How to install ROS](http://www.ros.org/install/) 

**`NOTE`**: These instruction was tested on Ubuntu 14.04 LTS with ROS Indigo and Ubuntu 16.04 LTS with ROS Kinetic.
**`WARNING`** chose correct version of ROS based on version of your Ubuntu.

---

### Network Connection

There are two different methods to access the AgriBot's on-board PC (Raspberry Pi), via (a) Wifi and (b) Ethernet connection. 

**`NOTE`** In case you want to run expensive algorithms like online mapping or
record the data from vision sensors, its recommended to use the Ethernet
connection as it is more reliable and provides more speed.

**`WARNING`** If you want to take the robot outside of the lab, you must connect to the Ethernet switch which is mounted on the robot. Currently, WiFi connection is not supported outside the lab. 

For both WiFi and Ethernet connections, we will set the network properties as shown in the image below:

<div align="center">Network-connection</div>

To find more information about multiple machine structure in ROS visit [MultipleMachines](http://wiki.ros.org/ROS/Tutorials/MultipleMachines).

#### Wifi Connection

We first need to set the IP address of the remote PC as the ROS_HOSTNAME in
order to enable communication between AgriBot on-board PC (Raspberry Pi) and
the remote PC. Make sure that the remote PC and AgriBot PC should be connected
to the same WiFi network. 

Enter the command below in terminal window of the remote PC to find out the IP
address of the remote PC.

```
$ ifconfig
```
Enter this command to open the .bashrc file with nano editor in terminal.

```
$ nano ~/.bashrc
```

Press `alt+/` to jump to the end line of the file.
Add these two lines to modify the address of local host in the `ROS_MASTER_URI` and `ROS_HOSTNAME`. 

```
# set raspi as the master#
export ROS_MASTER_URI=http://131.220.233.190:11311
export ROS_HOSTNAME=(IP OF REMOTE PC for example: 131.220.233.191)
```

* save the changes and to exit press */Ctrl + x*.

Then, source the bashrc with command below.

```
$ source ~/.bashrc
```

**`NOTE`**
Special Cases:
1) If you want to run the remote PC as both `ROS Master` and the host, both IP addresses (`ROS_MASTER_URI` and `ROS_HOSTNAME`) should be set equal to your IP address (on the remote PC)

2) If you're going use Agribot PC (raspberry pi) as ROS master both IP addresses (`ROS_MASTER_URI` and `ROS_HOSTNAME`) should be set equal to Agribot's IP address.

please pay attention to this [Network config](https://github.com/PRBonn/Agribot/raw/master/doc/images/wifi.png)

#### Ethernet Connection

To the Ethernet connection, first connect the remote PC via the Ethernet cable to the switch mounted on the robot. 
Next, set the IP address of your PC manually in the range of 196.168.0.x (except 196.168.0.100 as its used for robot):

After connecting the Ethernet cable, please follow below instructions:

- Test if the connection is properly made: (you should find the IP address of your PC in streamed text)

```
$ ifconfig
```
make sure specified IP address is shown under title of Ethernet connection.

Enter the below command to open the .bashrc file with nano editor in terminal.

```
$ nano ~/.bashrc
```

Press `alt+/` to jump to the end line of the file.
Add these two lines to modify the address of local host in the `ROS_MASTER_URI` and `ROS_HOSTNAME`.
```
# set raspi as the master#
export ROS_MASTER_URI=http://192.168.0.100:11311
export ROS_HOSTNAME=(IP OF REMOTE PC for example: 192.168.0.101)

```

Then, source the bashrc with below command.

```
$ source ~/.bashrc
```

**`NOTE`**
Special Cases:
1) If you want to run the remote PC as both `ROS Master` and the host, both IP addresses (`ROS_MASTER_URI` and `ROS_HOSTNAME`) should be set equal to your IP address (on the remote PC)

2) If your going use Agribot PC (raspberry pi) as ROS master both IP addresses (`ROS_MASTER_URI` and `ROS_HOSTNAME`) should be set equal to Agribot's IP address.

**`NOTE`**
In case of hving any problem with network connections check the [Debug The Network Connection](https://github.com/PRBonn/agribot/blob/master/doc/dedug.md#debug-the-network-connection).

---

### Logging into AgriBot
There are two different ways to access the OS running on the AgriBot PC:

#### Log into AgriBot PC using HDMI display
Simply use the HDMI port on the raspberry pi to stream out the display data. 

**`NOTE`** The user-name and password of AgriBot's local process is:
* USER-Name: igg
* Password: 12345

**`NOTE`** In the default mode, the raspberry Pi is booting without displaying the
Desktop to make it faster, in case of needing the desktop application use
*raspi-config* command to bring up the configure windows and in boot option
menu, you can change the mode of boot to *desktop*. more information about
[*raspi_config*](https://www.raspberrypi.org/documentation/configuration/raspi-config.md)

#### Log into AgriBot PC using SSH connection
this tool gives you this option to log into a remote PC from the terminal.
to log into AgriBot local processor use command below:

**Ethernet**
```
ssh igg@192.168.0.100
```
**WiFi**
```
ssh igg@131.220.233.190
```

Following are the login details for the AgriBot PC:
* USER-Name: igg
* Password: 12345

You can find more information about [SSH connection](https://help.ubuntu.com/community/SSH/OpenSSH/ConnectingTo). 

#### Using Screen Tool (Recommended for longer runs)

Use the screen tool in case which you want to disconnect your system or
shutdown the SSH connection and still have all the nodes running on the
AgriBot local PC. Screen is a console application that allows you to use
multiple terminal sessions within one window. The program operates within a
shell session and acts as a container and manager for other terminal sessions,
similar to how a window manager manages windows.[Reference
Link](https://www.digitalocean.com/community/tutorials/how-to-install-and-use-screen-on-an-ubuntu-cloud-server)

**How to install screen**

Use “apt-get” to install on Ubuntu:
```
sudo apt-get update
sudo apt-get install screen
```
Run the application on terminal:

```
screen
```
**`NOTE`** To use the screen tool to run the nodes on AgriBot, just run the
command screen before running SSH commands on your own PC.

#### Run the *roscore*

In case you need to debug or develop a code, its better to run the `roscore`
separately to have it always running. Otherwise is each time you want to run
your program (using launch files) you will need to shutdown all nodes like
simulators or dependent nodes which you had run before, because they won't
recognize new roscore.

But, if you just want to run the robot and record data or have test, you don't need to run `roscore` separately.

To Run the ROS_MASTER run this command on your PC or on the Raspberry Pi:
```
$ roscore
```
more information about *roscore* in [ROS Wiki](http://wiki.ros.org/roscore). 

#### Run the Base Controller of AgriBot

Now we will run all nodes required to record data and drive the robot.

<!-- to run this command in case which you have run the *roscore* earlier, open
another terminal tab with `<Shift+Ctrl+T>` and follow instruction in part
[SSH](https://github.com/PRBonn/agribot/blob/master/doc/connect.md#log-into-agribot-pc-using-ssh-connection).
 -->

```
$ roslaunch agribot_launch base.launch
```

**`NOTE`** In starting time of the base, buzzer will make 2 short beeps (to indicate that base is launched). After hearing the beeps you should wait 5 ~ 10 seconds to be able to drive the robot (this time is necessary to establish the connection between embedded-ROS nodes).

**`NOTE`**
if after launching the robot base controller you get any error like:

```xml
[ERROR] [1549010158.867290]: Unable to sync with device; possible link problem or link software version mismatch such as hydro rosserial_python with groovy Arduino
```
don't pay attention to it, this is a unsolved package issue from the main developers, but the robot will work without any problem. its recommanded to check th topics to make sure of working fine, too.

If all the nodes launch without an error, robot is ready to be
moved/controlled by joystick or some other nodes publishing */cmd_vel* topic.

More information about the packages and launch files are available in [AgriBot Software](https://github.com/PRBonn/agribot/blob/master/doc/api.md) section. 

**`NOTE`**
In case you don't used *base.launch* from *agribot_launch* package, you should
launch each node separately for sensors and actuators. for more
information about the *launch* files refer to [*agribot_launch*](https://github.com/PRBonn/agribot/blob/master/doc/api/agribot_launch.md)

**`NOTE`**  
If connection between Raspberry Pi and motor drivers (from motors) couldn't be
established correctly (in any case of having problem in connection or power or
etc...) relays on the robot will begin to switch on and off and buzzer will
make sound.

---

## How to Use JoyStick

to drive the robot with joystick, you should first launch agribot_joystick.launch file with command below:

```xml
roslaunch agribot_joystick agribot_joystick.launch
```
**`WARNINIG`** while testing the motion of the robot keep your distance from the robot. its better to stand on side of the robot. also the front of the robot is where the Zed camera is mounted.

There are two modes to control the robot:
 - Indoor Mode  : Low power mode for indoor operations. (Activation with Indoor-Deadman button)
 - Outdoor Mode : High power mode for outdoor operations. (Activation with Outdoor-Deadman button)

Indoor mode provides less power to motors whereas outdoor which uses maximum
power (These parameters can be modified through *config.yaml* files on the
*agribot_joystick* package).

Functionality of different buttons is shown in the image below:

<div align="center">
	JoystickTop
	JoystickFront JoystickTop
</div>

As simple instructions to drive the robot:

1. hold Indoor-Deadman button and try to drive the robot forward and backward by give some throttle (on left throttle axis - marked as linear Velocity).
2. while holding Indoor-Deadman button and linear velocity axis pressed, To drive the robot to the left and right, push the Steering-axis (marked as Steering angle) and hold it while robot is moving. 

**`NOTE`** if you releasing the Steering axis, wheels will go back to central position, similarly for linear velocity axis, robot will move as long as the throttle has some angle. On top of all functionalities Deadman button should always be pressed too.

For more information about joystick refer to [*agribot_joystick*](https://github.com/PRBonn/agribot/blob/master/doc/api/agribot_joystick.md)

---

### How to Record Data

You can record a bag file using the following command:

*Example_1:* To record all topics in home folder:
```
$ rosbag record -a
```
*Example_2:* To suppress a topic:
```
$ rosbag record -q /chatter
```
```
$ rosbag record -O <place for the address of  hosting location to save the bag file with name.bag > <place to list of your topics to record, in case of wanting all topics to be recorded use -a >
for instance:
$ rosbag record -O Agribot_sugarbeet.bag /chatter
or:
$ rosbag record -O Agribot_sugarbeet.bag -a
```

The recorded data can be saved either on AgriBot local processor (which only
contains 32GB of storage) or on the remote PC.
To ease the recording process you can use a launch file with necessary
commands located on agribot_launch package. More description in [AgriBot
Software](https://github.com/PRBonn/agribot/blob/master/doc/api.md)
section.

More information about recording bag file [ROS bag file](http://wiki.ros.org/rosbag/Commandline)

**`NOTE`** In case of recording sensors with dense output like Z-Camera or
Lidar, its recommended to use remote PC as main host for bag file. Otherwise
AgriBot processor will run out of storage and crash.

**`WARNING`** while recording bag files and driving robot around for long
time, keep checking all the connections, the status of ROS network, charge of
battery, because sometimes due to network faults or failures in electrical
connections bag files won't be usable at the end. (these cases happen when
robot has a electrical problem or there is some defects in ROS network or
sensor connections to remote PC, so its better to check them first!!!)

---

### How to Turn-Off the robot

to shutdown the robot first run the command below, to shutdown the raspberry pi and then swtich of both power keys shown in [here](https://github.com/PRBonn/Agribot/raw/master/doc/images/powerswitch.png)

```
sudo poweroff
```
---

[The Main ReadMe](https://github.com/PRBonn/agribot/blob/master/README.md)

*Section* 
- [Mechanical Design](https://github.com/PRBonn/agribot/blob/master/doc/mec.md)
- [Electrical  Design](https://github.com/PRBonn/agribot/blob/master/doc/elec.md)
- [AgriBot Software](https://github.com/PRBonn/agribot/blob/master/doc/api.md) 
- [Debug](https://github.com/PRBonn/agribot/blob/master/doc/debug.md)

--- 
 by: [Alireza Ahmadi](https://github.com/alirezaahmadi)                                     
 University of Bonn- Robotics & Geodetic Engineering

 Alireza.Ahmadi@uni-bonn.de

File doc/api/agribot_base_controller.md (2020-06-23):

# AgriBot Project (Servo Controller)

<!-- <div align="center">
	<img src="/doc/images/joystick_top.png" alt="JoystickTop" width="450" title="JoystickTop"/>
</div> -->

---

## Table of Contents
- [Kinamtics of Agribot](https://github.com/PRBonn/agribot/blob/master/doc/api/agribot_base_controller.md#kinamtics-of-agribot)
  - [About the *agribot_base_controller* package](https://github.com/PRBonn/agribot/blob/master/doc/api/agribot_base_controller.md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)
  - [Driving front Wheels](https://github.com/PRBonn/agribot/blob/master/doc/api/agribot_base_controller.md#1driving-front-wheels)
  - [Kinematics model](https://github.com/PRBonn/agribot/blob/master/doc/api/agribot_base_controller.md#2kinematics-model)
  - [Providing Odometry data](https://github.com/PRBonn/agribot/blob/master/doc/api/agribot_base_controller.md#3providing-odometry-data)
  - [Handling The Errors and Alarms](https://github.com/PRBonn/agribot/blob/master/doc/api/agribot_base_controller.md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)
  - [How to Launch *agribot_base_controller*](https://github.com/PRBonn/agribot/blob/master/doc/api/agribot_base_controller.md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)

---

## Kinamtics of Agribot

In standard vehicles, front wheels are driven and the car is steered by changing their direction which it means the rear wheels are just pulled by torque generated from front wheels. In this configuarion, back wheels are just used to hold car balanced and increase the maneuverability. In AgriBot platform, rear wheels are used to steer the robots motion and front wheels are driven by two geared DC motors. Generally, vehicles with streering system at the back are used in cases which high maneuverability is necessary on low-speed mode, such as forklifts. The steerable wheels of the AgriBot are able to turn more than 90deg to the left and right. Such a robot is highly maneuverable at a low speed. To properly controll a four-wheel vehicle like AgriBot, one constraint needs to be hold to let inner and outer wheels turn slip- free.

<div align="center">
  KDrive
  constraint
</div>
where, δi and δo are inner and outer steer angles, respectively.

## About the *agribot_base_controller* package

This package contains all the dependencies and implementations related to driving the front wheels and the implementation of the kinematic model. The main core is based on [md49_base_controller](http://wiki.ros.org/md49_base_controller) which some modifications and improvements are applied to customize it for Agribot platform.

### 1.Driving front Wheels
This package comes with the name of *md49_base_controller* and offers functions to connect to the MD49 embedded drivers. AgriBot platform is equipped  with two geared DC-motors and respectively two drivers which, are controlled by the Raspberry Pi (Local processor on AgriBot) via USB (Virtual Com-Port). Image below shows the driver and actuator model with related links.

<div align="center">
  EMG49
  MD49
</div>

* [Driving motors - EMG49](https://robot-electronics.co.uk/products/drive-systems/emg49-gearmotor-with-encoder.html)
* [front wheel's Driver - MD49](https://robot-electronics.co.uk/md49-24v-5a-dual-h-bridge-motor-driver.html)

The image below shows all connections related to front actuators. 

<div align="center">
  md49con
</div>

### 2.Kinematics model

As it's mentioned earlier it dose all the calculations related to the kinematics of the robot. This means, its always subscribing to the */cmd_vel* topic (topic which provides velocity fields), and converts them to proper data to feed the drivers. Here, as the motion is dependent of actuation of front and back wheels, package needs to publish on the topic */servo_poses* which is subscribed by *agribot_servo* to orient back wheels properly with respect to the desired velocities and used kinematics model.

The implementation of different kinematic models are done in a library called *agribt_kinematics.h* which already contains three different kinematic models (differential model, Ackermann model, improved Ackermann model) and is switchable by the user. 

*`NOTE`* the default kinematic model which performs the best, is the *Improved Ackermann*, and its recommended to be used. Also the differential model is not usable with new structures implemented for back wheels.

to change the kinematic model, change the value of *KinematicModel* as a variable defined in *agribt_kinematics.h*. this parameter is not available as *ros-param* variable because its not supposed to  change a lot.

the orientation of local coordinate system on the robot which odometry will use it is shown in figure below.

<div align="center">
  robot_coordinate
</div>

### 3.Providing Odometry data

This package provide the odometry data from different sources (wheel odometry and mocap odometry) along with driving the robot. 

* The mocap odometry is available if the robot is running in the lab with mocap system running and publishing the topic */amcl_pose* as the 2D/3D position of the robot and the functions in the *agribt_kinematics.h* converts it to odometry data, also initializes the wheels odometry at the beginning if its available.
* wheels odometry always is available and is published on its specific topic too.

*`NOTE`* as long as the wheels odometry data is dependent of kinematics model, its recommended to use *Improved-Ackermann* model because its prividing more accurate odomatry data. images below shows the odomatery results of *Ackermann* and *Improved-Ackermann* models.
* Green track is the mocap odomtery, as ground truth, and in the left image the *Ackermann* models odometry is shown beside *Improved-Ackermann* models odometry on the right.

<div align="center">
  ackerodom
  ackermmImproved
</div>

for more information about *mocap* system refer to this page [Motion Capture](https://github.com/PRBonn/agribot/blob/master/doc/api/mocap.md) 

### 4. Handling The Errors and Alarms
As it has access to Drivers and their registers (internal variables/status like voltage, temperature, etc...) its able to detect errors and make some proper actions to solve the problem or warn them through alarms.  therefore, two relays are controlled by this node which are actually controlling the power of actuators. This means, in case of having any problem in connection it could restart the drivers and re-establish the connections to the  drivers, also it makes some alarms via a buzzer. form more information about the Relays and Buzzers and their electrical connections refer to [*AgriBot Electrical Design*](https://github.com/PRBonn/agribot/blob/master/doc/elec.md)

### How to Launch *agribot_base_controller*
To launch it simply run: 

```
$ roslaunch md49_base_controller md49_base_controller_local.launch
```
**`NOTE`** In starting time of the base, buzzer will make 2 short beeps (to indicate that base is launched). After hearing the beeps you should wait 5 ~ 10 seconds to be able to drive the robot (this time is necessary to establish the connection between embedded-ROS nodes).

Node [/md49_base_controller]

**Publications**: 
 * /ServoPose [std_msgs/Int16MultiArray]
 * /md49_data [md49_messages/md49_data]
 * /md49_diff [md49_messages/md49_diff]
 * /md49_encoders [md49_messages/md49_encoders]
 * /mocap_odom [nav_msgs/Odometry]
 * /odometry/raw [nav_msgs/Odometry]
 * /rosout [rosgraph_msgs/Log]
 * /tf [tf2_msgs/TFMessage]

**Subscriptions**: 
 * /amcl_pose [unknown type]
 * /cmd_vel [unknown type]
 * /md49_diff [md49_messages/md49_diff]
 * /md49_encoders [md49_messages/md49_encoders]

**Services**: 
 * /md49_base_controller/get_loggers
 * /md49_base_controller/set_logger_level

--- 

**Parameters**
 * /md49/acceleration: 4
 * /md49/mode: 0
 * /md49/regulator: True
 * /md49/speed_l: 128
 * /md49/speed_r: 128
 * /md49/timeout: True
 * /serialport/bps: 38400
 * /serialport/name_l: /dev/md49_l
 * /serialport/name_r: /dev/md49_r

---

*`NOTE`* this package can't be built on any remote PC completely, due to using some native libraries of Raspberry Pi like [*WiringPi*](http://wiringpi.com) to control GPIO pins.

--- 
* [The Main ReadMe](https://github.com/PRBonn/agribot/blob/master/README.md)
* [AgriBot Software](https://github.com/PRBonn/agribot/blob/master/doc/api.md) 

--- 
 by: Alireza Ahmadi                                     
 University of Bonn- Robotics & Geodetic Engineering
 
 Alireza.Ahmadi@uni-bonn.de                             
 []()

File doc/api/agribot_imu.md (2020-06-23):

# AgriBot Project (IMU)

---

## Table of Contents
- How to Use *agribot_imu*
  - [About the IMU Sensor](https://github.com/PRBonn/agribot/blob/master/doc/api/agribot_imu.md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)
  - [About the agribot_imu package](https://github.com/PRBonn/agribot/blob/master/doc/api/agribot_imu.md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)
  - [How to Launch *agribot_imu*](https://github.com/PRBonn/agribot/blob/master/doc/api/agribot_imu.md#how-to-launch-agribot_imu)
  - [How to Access/Modify Arduino code](https://github.com/PRBonn/agribot/blob/master/doc/api/agribot_imu.md#how-to-accessmodify-arduino-code)
  - [References](https://github.com/PRBonn/agribot/blob/master/doc/api/agribot_imu.md#references)

---

### About the IMU Sensor (Bosch - BNO-055 MEMS IMU Sensor)
If you've ever ordered and wire up a 9-DOF sensor, chances are you've also realized the challenge of turning the sensor data from an accelerometer, gyroscope and magnetometer into actual "3D space orientation"! Orientation is a hard problem to solve. The sensor fusion algorithms (the secret sauce that blends accelerometer, magnetometer and gyroscope data into stable three-axis orientation output) can be mind-numbingly difficult to get right and implement on low cost real time systems.

Bosch is the first company to get this right by taking a MEMS accelerometer, magnetometer and gyroscope and putting them on a single die with a high speed ARM Cortex-M0 based processor to digest all the sensor data, abstract the sensor fusion and real time requirements away, and spit out data you can use in quaternions, Euler angles or vectors.

Rather than spending weeks or months fiddling with algorithms of varying accuracy and complexity, you can have meaningful sensor data in minutes thanks to the BNO055 - a smart 9-DOF sensor that does the sensor fusion all on its own!  You can read the data right over I2C and Bob's yer uncle.

IMU Demo (from Adafruit)

The BNO055 can output the following sensor data:

* Absolute Orientation (Euler Vector, 100Hz) Three axis orientation data based on a 360° sphere
* Absolute Orientation (Quaterion, 100Hz) Four point quaternion output for more accurate data manipulation
* Angular Velocity Vector (100Hz) Three axis of 'rotation speed' in rad/s
* Acceleration Vector (100Hz) Three axis of acceleration (gravity + linear motion) in m/s^2
* Magnetic Field Strength Vector (20Hz) Three axis of magnetic field sensing in micro Tesla (uT)
* Linear Acceleration Vector (100Hz) Three axis of linear acceleration data (acceleration minus gravity) in m/s^2
* Gravity Vector (100Hz) Three axis of gravitational acceleration (minus any movement) in m/s^2
* Temperature (1Hz) Ambient temperature in degrees Celsius

<!-- <div align="center">
	<img src="/doc/images/logicbat_1.png" alt="logicbat_1" width="200" title="Logic power battery switch"/>
</div>  -->

### Dimensions and Electrical Specifications
* Dimensions: 20mm x 27mm x 4mm / 0.8" x 1.1" x 0.2"
* Header holes begin 4mm from the mounting holes
* Mounting Hole dimensions: 20mm x 12mm apart
* Uses I2C address 0x28 (default) or 0x29
* Weight: 3g
* Operating voltage: 3.3-5v
* Operating current: max 100mA

### Electrical Connection to System

In AgriBot, there are tow units which are operated based on *Embedded-ROS* which officially its called (Ros-Serial)[http://wiki.ros.org/rosserial ]. IMU module uses a *Arduino-ProMicro* board to access the raw values provided by the sensor. The connection used in this section is shown in image below:

<div align="center">BMS</div>

* As shown in the image the i2c protocol is used to connect the sensor module to arduino board which uses (SDA, SCL,VCC,GND) pins.
* Pin-out of *Arduino-ProMicro* and axes of BNO-055 can be found here:

<div align="center">
	pro-micro pinout
	BN axes
</div>

**`NOTE`**
if after launching the robot base controller you get any error like:

```xml
[ERROR] [1549010158.867290]: Unable to sync with device; possible link problem or link software version mismatch such as hydro rosserial_python with groovy Arduino
```
don't pay attention to it, this is a unsolved package issue from the main developers, but the robot will work without any problem. its recommanded to check th topics to make sure of working fine, too.

---

### About the *agribot_imu* package (Embedded-ROS)

**`NOTE`**
In case which you want to access the IMU data via using AgriBot local processor, you can skip next part and jump to [How to launch *agribot_imu*](https://github.com/PRBonn/agribot/blob/master/doc/api/agribot_imu.md#how-to-launch-agribot_imu).

In case you want to use the IMU module with another PC, please follow these steps:

1. Connect the module via Micro-USB  cable to PC.
2. Check the Com-Port name in:
```
$ cd /dev/ &
$ ls 
```
based on the name you find, using above command, change the Com-Port name in file 'imu.launch'.

```xml
<?xml version="1.0"?>
<launch>
	<node pkg="rosserial_python" type="serial_node.py" name="agribot_imu">
		<param name="port" value="/dev/imu"/>
		<param name="baud" value="57600"/>
	</node>	
</launch>
```
Now you're ready to launch the node. please keep no the tutorials.

---

## How to launch *agribot_imu*

To launch the *agribot_imu* simply run: 

```
$ roslaunch agribot_launch imu.launch
```
In case which everything working correctly, the terminal should print out relative information. please attention to image below:

<!-- <div align="center">
	<img src="/doc/images/logicbat_1.png" alt="logicbat_1" width="200" title="Logic power battery switch"/>
</div>  -->

Node name : /agribot_imu

Publications: 
 * /imu (sensor_msgs/imu)

Subscriptions: 
 * None

Services: 
 * None

--- 

**Parameters**
 * None

--- 

### How to Access/Modify Arduino code

To modify the #agribot_imu* code, you should install [Arduino compiler](https://www.arduino.cc) or its plug-in on sublime [Arduin On Sublime](https://packagecontrol.io/packages/Arduino-like%20IDEarduino) and useful tutorial are given in Arduino website as well.

You can access the #agribot_imu* code via link below:
* [AgriBot-IMU code](https://github.com/PRBonn/Agribot/tree/master/code/agribot_imu)

---
* [The Main ReadMe](https://github.com/PRBonn/agribot/blob/master/README.md)
* [AgriBot Software](https://github.com/PRBonn/agribot/blob/master/doc/api.md) 

---
### References
- [Adafruit Website](https://www.adafruit.com/product/2472)

--- 
 by: Alireza Ahmadi                                     
 University of Bonn- Robotics & Geodetic Engineering
 
 Alireza.Ahmadi@uni-bonn.de                             
 []()

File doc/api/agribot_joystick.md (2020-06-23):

# AgriBot Project (Joystick)

<!-- <p align="center"><img src="https://cdn.discordapp.com/attachments/205245036084985857/481213000540225550/full_example.gif" /></p> -->

---

## Table of Contents
- [How to Use JoyStick]()
  - [About the *agribot_joystick* package](https://github.com/PRBonn/agribot/blob/master/doc/joystick.md#about-the-agribot_joy-package)
  - [Buttons/Axis functionalities](https://github.com/PRBonn/agribot/blob/master/doc/api/agribot_joystick.md#buttonsaxis-functionalities)

---

**`WARNING`** 
- always make sure your distance to the robot is less than 20 meters.
- In case of noticing any delay in responds from robot, restart the nodes.

---

### About the *agribot_joystick* package
the main package to establish connection between Joystick and Raspberry Pi on the robot is *joy_teleop* [github](https://github.com/ros-drivers/joystick_drivers/tree/master/joy) which is provided by ROS. The package *agribot_joystick* in up to generate specific velocity commands. 

To launch the joystick simply run: 
```
$ roslaunch agribot_joystick agribot_joystick.launch
```

**NOTE** its better to check battery of joystick before launching the node. in case of joystick being not connected/recognized node will throw some error on the screen.

Node name : /agribot_joystick

Publications: 
 * /ServoPose [std_msgs/Int16MultiArray]
 * /cmd_vel [geometry_msgs/Twist]
 * /rosout [rosgraph_msgs/Log]

Subscriptions: 
 * /joy [sensor_msgs/Joy]

Services: 
 * /agribot_joystick/get_loggers
 * /agribot_joystick/set_logger_level

---

### Buttons/Axis functionalities

button and axis on the joystick can control the linear and angular velocities of the robot in two different modes (indoor and outdoor) 
 - indoor mode has provides less power to motors than outdoor which uses maximum power (these parameters can be modified through config/.yaml files on the package).

functionality of each input is show in image below:

<div align="center">
	JoystickTop
	JoystickFront JoystickTop
</div>

As simple instructions to drive the robot:

1. hold Indoor-Deadman button and try to drive the robot forward and backward by give some throttle (on left throttle axis - marked as linear Velocity).
2. while holding Indoor-Deadman button and linear velocity axis pressed, To drive the robot to the left and right, push the Steering-axis (marked as Steering angle) and hold it while robot is moving. 

**NOTE** if you releasing the Steering axis, wheels will go back to central position, similarly for linear velocity axis, robot will move as long as the throttle has some angle. On top of all functionalities Deadman button should always be pressed too.

--- 

**Parameters**

* Tur_lin_scale (double, default: 2)
The amount to scale the joystick input for the command linear velocity output in turbo(outdoor) mode.
* Tur_ang_scale (double, default: 1)
The amount to scale the joystick input for the command angular velocity output in turbo(outdoor) mode.

* lin_scale (double, default: 0.25)
The amount to scale the joystick input for the command linear velocity output.
* ang_scale (double, default: 1.5)
The amount to scale the joystick input for the command angular velocity output.
* srv_scale (double, default: 90)
The amount to scale the joystick input for the command velocity output.

* axis_deadman (int, default: 5)  # L2 shoulder button
The joystick index to disables/enables the output cmd_vel message(indoor).
* axis_turbo (int, default: 4)   # L1 shoulder button
The joystick index to disables/enables the output cmd_vel message(outdoor).
* axis_servo (int, default: 6)   
The joystick index to disables/enables the output servo (steering wheels joints) message.
* axis_stop (int, default: 7)   
The joystick index to disable the output cmd_vel and reset position of servos.

* axis_linear (int, default: 1)
The joystick button index to control linear speed
* axis_angular (int, default: 2)
The joystick button index to control angular speed
* axis_servo (int, default: 0)
The joystick button index to control position of steering system (servos)

--- 
* [The Main ReadMe](https://github.com/PRBonn/agribot/blob/master/README.md)
* [AgriBot Software](https://github.com/PRBonn/agribot/blob/master/doc/api.md) 

--- 
 by: Alireza Ahmadi                                     
 University of Bonn- Robotics & Geodetic Engineering
 
 Alireza.Ahmadi@uni-bonn.de                             
 []()

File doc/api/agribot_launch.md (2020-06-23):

# AgriBot Project (launch)

---

### About the *agribot_launch* package
This package is a collection of all *.launch* files from all packages written for AgrBot robot. 

To launch one desired launch file from this package simply run:
```
$ roslaunch agribot_launch YOUR_DESIRED_LAUNCH_FILE.launch
```
here is a list of all important launch files stored in */launch* folder of this package:

1. **base.launch** is the main launch file to run the necessary packages to drive the robot. it is a collection of drive.launch, sensors.launch and etc..
2. **gps.launch** launches the gps node to connect to the U-blox module which is a PPP GPS antenna and receiver.
3. **zed.launch** runs the Zed camera node, and streams all types of images and topics into ROS platform.
4. **camera.launch** uses *uvc_camera* pckage to get the images from an input camera/webcam from specific port and with special resolution which are defined in the launch file.
5. **imu.launch** creates a Embedded-ROS node using a python package called *rosserial_python* and opens the */dev/imu* port to access the imu data. more information in [*agribot_imu*](https://github.com/PRBonn/agribot/blob/master/doc/api/agribot_imu.md)
6. **xsens_driver.launch** drives the xsens IMU sensor which should be connected to one of the Raspberry Pi USB ports. 
7. **servo.launch** creates another Embedded-ROS node to access the Stepper-Drivers to control rear caster wheels. for more information take a look at [*agribot_servo*](https://github.com/PRBonn/agribot/blob/master/doc/api/agribot_servo.md)
8. **px4flow.launch** launches a node to access the odometry data provided by *px4flow* sensor which runs an embedded-optical flow.
9. **drive.launch** launches nodes required to make the connection to all actuators in the back and front of the robot. Also launches the joystick to user be able to run the robot independently.
10. **sensors.launch** a collection of commands to launch all the sensors which might be running for a specific test.

--- 
* [The Main ReadMe](https://github.com/PRBonn/agribot/blob/master/README.md)
* [AgriBot Software](https://github.com/PRBonn/agribot/blob/master/doc/api.md) 

--- 
 by: Alireza Ahmadi                                     
 University of Bonn- Robotics & Geodetic Engineering
 
 Alireza.Ahmadi@uni-bonn.de                             
 []()

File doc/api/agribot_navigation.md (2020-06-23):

# AgriBot Project (Navigation)

---

 - [Navigation In ROS](https://github.com/PRBonn/agribot/blob/master/doc/api/agribot_navigation.md#navigation-in-ros)
 - [Navigation in AgriBot](https://github.com/PRBonn/agribot/blob/master/doc/api/agribot_navigation.md#navigation-in-agribot)
 - [About the *agribot_navigation* package](https://github.com/PRBonn/agribot/blob/master/doc/api/agribot_navigation.md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)
 	- [The *move_base* package](https://github.com/PRBonn/agribot/blob/master/doc/api/agribot_navigation.md#the-move_base-package)
 	- [How to run navigation base](https://github.com/PRBonn/agribot/blob/master/doc/api/agribot_navigation.md#how-to-run-navigation-base)
 	- [About the *map_server* Package](https://github.com/PRBonn/agribot/blob/master/doc/api/agribot_navigation.md#about-the-map_server-package)
 		- [how to set an image as predefined/input map:](https://github.com/PRBonn/agribot/blob/master/doc/api/agribot_navigation.md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)
 - [References](https://github.com/PRBonn/agribot/blob/master/doc/api/agribot_navigation.md#references)

---

## Navigation In ROS
This package contains the most important parameters to run the [Navigation](http://wiki.ros.org/navigation) package from ROS.
It is A 2D navigation stack that takes in information from odometry, sensor streams, and a goal pose and outputs safe velocity commands that are sent to a mobile base.

It takes in information from odometry and sensor streams and outputs velocity commands to send to a mobile base. As a pre-requisite for navigation stack use, the robot must be running ROS, have a tf transform tree in place, and publish sensor data using the correct ROS Message types. Also, the Navigation Stack needs to be configured for the shape and dynamics of a robot to perform at a high level.

<div align="center">
	navgraph
</div>

more information in [Navigation](http://wiki.ros.org/navigation)

---

## Navigation in AgriBot

The path which robot should traverse on its operations in the field could be divided into different motion/action which, behavior core will execute assorted strategies and distinct algorithms to fulfill the tasks. As figure below shows, navigation is divided into three major steps which includes way-point navigation, Turning action to switch between the rows in the field and VisualServoing navigator which guides the robot through crop rows. 

<div align="center">
	navgraph
</div>

If we suppose, the robot starts from the beginning of a crop row in the field, the desire is to approaching to a different known positions on the other side of the row through navigating between crop rows. This part is defined between different way-points (known points) which locally or globally their positions are recorded in such a way that user can redefine or adjust them. 

The robot’s motion will be controlled by VisualServoing and a local planner core through the path between these two way-points. This means the core of this navigation strategy is the VisualServoing and the local planner packages, which process all the sensory data and decisions are made based actions needed to be performed. 

<div align="center">
	navgraph
</div>

as its shown in the figure, almost all the sensors and actuators are used in this process. Also, performing different variants of one specific action is possible with different ground truth or different motion sensors ( for example: odometry from wheel, *mocap* or visual). Onward, user can use the fusion of sensors thorough localization package which tries to fuse all sensory data to reach a more reliable one.

* more information about [*agribot_localization*](todo...) package.

* [agribot_visualservoing](https://github.com/PRBonn/agribot/blob/master/doc/api/agribot_visualservoing.md)
* [agribot_local_planner](https://github.com/PRBonn/agribot/blob/master/doc/api/agribot_local_planner.md)

Also, the behavior core on top of all nodes will manage to turn the robot toward next row at the end of each row and switch the controllers properly. 

The turning action can be generated by the local planner and some static steps of motion defined by the user. at the moment one static trajectory (in shape of circle) is defining steps which takes the robot from one row to another.

<div align="center">
	navgraph
</div>

Also, the operator can control the robot while it is performing an action by [joystick](https://github.com/PRBonn/agribot/blob/master/doc/api/agribot_joystick.md). 

Assume, a goal is given to the robot, in the robot’s environment (coordinate system), the local planner core along with *move_base* package provides a plan that endeavors to get the robot to it. 

In the background of navigation stack operation, there is a global planner which generates the required trajectory based on a variant of the A* algorithm. So far, the navigation implementation illustrated with two different layers, global and local planners which global planner plans the path to the target and local planner attempts to drive the robot toward the goal using VisualServoing and other actions. 

These layers specially the global planner could be defined specially for AgroBot which its core is under development.

## About the *agribot_navigation* package
The navigation package is containing map dependencies, Navigation stack parameters(move_base, planners,...) and a simple node to send static goals to robot along with simple launch files to ease the running process. the most important dependencies and packages are illustrated in following.

### The *move_base* package
The move_base package provides an implementation of an action (see the actionlib package) that, given a goal in the world, will attempt to reach it with a mobile base. The move_base node links together a global and local planner to accomplish its global navigation task.

In AgriBot project, *move_base* launches via *agribot_move.launch* from *agribot_navigation* package.

```
$ roslaunch agribot_navigation agribot_move.launch
```
Node [/move_base]
**Publications**: 
 * /cmd_vel [geometry_msgs/Twist]
 * /current_pose [geometry_msgs/PoseStamped]
 * /move_base/AgribotLocalPlanner/parameter_descriptions [dynamic_reconfigure/ConfigDescription]
 * /move_base/AgribotLocalPlanner/parameter_updates [dynamic_reconfigure/Config]
 * /move_base/NavfnROS/plan [nav_msgs/Path]
 * /move_base/current_goal [geometry_msgs/PoseStamped]
 * /move_base/feedback [move_base_msgs/MoveBaseActionFeedback]
 * /move_base/global_costmap/costmap [nav_msgs/OccupancyGrid]
 * /move_base/global_costmap/costmap_updates [map_msgs/OccupancyGridUpdate]
 * /move_base/global_costmap/footprint [geometry_msgs/PolygonStamped]
 * /move_base/global_costmap/parameter_descriptions [dynamic_reconfigure/ConfigDescription]
 * /move_base/global_costmap/parameter_updates [dynamic_reconfigure/Config]
 * /move_base/global_costmap/static/parameter_descriptions [dynamic_reconfigure/ConfigDescription]
 * /move_base/global_costmap/static/parameter_updates [dynamic_reconfigure/Config]
 * /move_base/goal [move_base_msgs/MoveBaseActionGoal]
 * /move_base/local_costmap/costmap [nav_msgs/OccupancyGrid]
 * /move_base/local_costmap/costmap_updates [map_msgs/OccupancyGridUpdate]
 * /move_base/local_costmap/footprint [geometry_msgs/PolygonStamped]
 * /move_base/local_costmap/parameter_descriptions [dynamic_reconfigure/ConfigDescription]
 * /move_base/local_costmap/parameter_updates [dynamic_reconfigure/Config]
 * /move_base/local_costmap/static/parameter_descriptions [dynamic_reconfigure/ConfigDescription]
 * /move_base/local_costmap/static/parameter_updates [dynamic_reconfigure/Config]
 * /move_base/parameter_descriptions [dynamic_reconfigure/ConfigDescription]
 * /move_base/parameter_updates [dynamic_reconfigure/Config]
 * /move_base/result [move_base_msgs/MoveBaseActionResult]
 * /move_base/status [actionlib_msgs/GoalStatusArray]
 * /rosout [rosgraph_msgs/Log]
 * /target_pose [geometry_msgs/PoseStamped]

**Subscriptions**: 
 * /map [nav_msgs/OccupancyGrid]
 * /mocap_odom [nav_msgs/Odometry]
 * /move_base/cancel [unknown type]
 * /move_base/global_costmap/footprint [geometry_msgs/PolygonStamped]
 * /move_base/goal [move_base_msgs/MoveBaseActionGoal]
 * /move_base/local_costmap/footprint [geometry_msgs/PolygonStamped]
 * /move_base_simple/goal [unknown type]
 * /tf [tf2_msgs/TFMessage]
 * /tf_static [tf2_msgs/TFMessage]

**Services**: 
 * /move_base/AgribotLocalPlanner/set_parameters
 * /move_base/NavfnROS/make_plan
 * /move_base/clear_costmaps
 * /move_base/get_loggers
 * /move_base/global_costmap/set_parameters
 * /move_base/global_costmap/static/set_parameters
 * /move_base/local_costmap/set_parameters
 * /move_base/local_costmap/static/set_parameters
 * /move_base/make_plan
 * /move_base/set_logger_level
 * /move_base/set_parameters

* from more informtion about *move_base*  package visit [ROS *move_base*](http://wiki.ros.org/move_base)

### How to run navigation base
To launch the *agribot_navigation* simply run: 
```
$ roslaunch agribot_navigation agribot_navigation.launch
```
it will publish the map via using *map_server* package and launches *move_base* including global and local planners.

**NOTE** it needs the */tf* to be published from base controller and robot description. [*agribot_base_controller*](https://github.com/PRBonn/agribot/blob/master/doc/api/agribot_base_controller.md), [*agribot_description*](todo...)

---

### About the *map_server* Package
map_server provides the map_server ROS Node, which offers map data as a ROS Service. It also provides the map_saver command-line utility, which allows dynamically generated maps to be saved to file

#### how to set an image as predefined/input map:
based on map_server tutorial on ros wiki, we can load an image as predefined or saved map which shows the environment is rigid cells in term of occupancy and this term can be archived by description in below.
The image describes the occupancy state of each cell of the world in the color of the corresponding pixel. In the standard configuration, whiter pixels are free, blacker pixels are occupied, and pixels in between are unknown. Color images are accepted, but the color values are averaged to a gray value.

here the YAML file which is defining characteristics of the map based on image use in Agribot navigation:

```yaml
image: map.png
resolution: 0.050000
origin: [0.000000, 0.000000, 0]
negate: 0
occupied_thresh: 0.65
free_thresh: 0.196
```

to run map dependencies in Agribot platfrom use:

```
$ roslaunch agribot_navigation agribot_map.launch
```

Required fields:

* *image* : Path to the image file containing the occupancy data; can be absolute, or relative to the location of the YAML file
* *resolution*: Resolution of the map, meters / pixel
* *origin* : The 2-D pose of the lower-left pixel in the map, as (x, y, yaw), with yaw as counterclockwise rotation (yaw=0 means no rotation). Many parts of the system currently ignore yaw.
* *occupied_thresh* : Pixels with occupancy probability greater than this threshold are considered completely occupied.
* *free_thresh* : Pixels with occupancy probability less than this threshold are considered completely free.
* *negate* : Whether the white/black free/occupied semantics should be reversed (interpretation of thresholds is unaffected)
Optional parameter:
* *mode* : Can have one of three values: trinary, scale, or raw. Trinary is the default. More information on how this changes the value interpretation is in the next section.

for more information take a look at [*map_server*](http://wiki.ros.org/map_server).

--- 

* [The Main ReadMe](https://github.com/PRBonn/agribot/blob/master/README.md)
* [AgriBot Software](https://github.com/PRBonn/agribot/blob/master/doc/api.md) 

---
## References
* [*map_server*](http://wiki.ros.org/map_server)
* [Navigation](http://wiki.ros.org/navigation)

--- 
 by: Alireza Ahmadi                                     
 University of Bonn- Robotics & Geodetic Engineering
 
 Alireza.Ahmadi@uni-bonn.de                             
 []()

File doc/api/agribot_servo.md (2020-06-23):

# AgriBot Project (Servo Controller)

---

## Table of Contents
- How to Use *agribot_srvo*
  - [About AgriBot's Rear Actators](https://github.com/PRBonn/agribot/blob/master/doc/api/agribot_servo.md#about-agribots-rear-actators)
  - [Electrical Connection to System](https://github.com/PRBonn/agribot/blob/master/doc/api/agribot_servo.md#electrical-connection-to-system)
  - [Serial to USB Converter](https://github.com/PRBonn/agribot/blob/master/doc/api/agribot_servo.md#serial-to-usb-converter)
  - [About the agribot_servo package (Embedded-ROS)](https://github.com/PRBonn/agribot/blob/master/doc/api/agribot_servo.md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)
  - [How to launch agribot_servo](https://github.com/PRBonn/agribot/blob/master/doc/api/agribot_servo.md#how-to-launch-agribot_servo)
  - [How to Access/Modify Arduino code](https://github.com/PRBonn/agribot/blob/master/doc/api/agribot_servo.md#how-to-accessmodify-arduino-code)
  - [References](https://github.com/PRBonn/agribot/blob/master/doc/api/agribot_servo.md#references)

---

### About AgriBot's Rear Actators 

AgriBot is equipped with two servos at the rear wheels which is servo controls the orientation of one of the wheels based on commands received from the motion controller node.  The motion controller is running under base_controller package. 

<div align="center">
	servocon
	gear
</div>

### Electrical Connection to System

In AgriBot, there are tow units which are operated based on *Embedded-ROS* which officially its called (Ros-Serial)[http://wiki.ros.org/rosserial ]. Servo controller module uses a *Arduino-Uno* board to controll the actuators via stepper drivers. The connection used in this section is shown in image below:

<div align="center">servocon</div>

* As shown in the image the some I/O pins are used to connect the stepper driver to the Arduino board which uses I/O pins listed in table below along with their functionality .

| Pins in Arduino  | Functionality | Connected to | 
| --- | --- | --- |
| 13  | LED | I/O  |
| A0  | Pin Num.2  | ADC - Left Potentiometer  |
| A1  | Pin Num.2  | ADC - right Potentiometer  |
| 5  | PUL | I/O  |
| 10  | DIR  | I/O |
| 6  | PUL  | I/O |
| 11  | DIR  | I/O  |

* Pin-out of *Arduino-Uno* and Schematic of Stepper-Driver  can be found here:

<div align="center">
	Uno pinout
	stepcon
</div>

#### Serial to USB Converter
USB/Serial Converter Turns a USB connection to the 5V TX and RX Arduino requires to communicate. This board converts a USB connection to the 5V TX and RX an Arduino requires for communication. You can connect straight to the Arduino Mini or other micro-controllers, allowing them to talk to the computer.

<div align="center">
	ft232rl
</div>

---

### About the *agribot_servo* package (Embedded-ROS)

**`NOTE`**
In case which you want to access the IMU data via using AgriBot local processor, you can skip next part and jump to [How to launch *agribot_imu*](https://github.com/PRBonn/agribot/blob/master/doc/api/agribot_imu.md#how-to-launch-agribot_imu).

In case you want to use the IMU module with another PC, please follow these steps:

1. Connect the module via Micro-USB  cable to PC.
2. Check the Com-Port name in:
```
$ cd /dev/ &
$ ls 
```
based on the name you find, using above command, change the Com-Port name in file 'servo.launch'.

```xml
<?xml version="1.0"?>
<launch>
  <node pkg="rosserial_python" type="serial_node.py" name="agribot_servo">
    <param name="port" value="/dev/servo"/>
  </node>
</launch>
```
Now you're ready to launch the node. please keep no the tutorials.

**`NOTE`**
if after launching the robot base controller you get any error like:

```xml
[ERROR] [1549010158.867290]: Unable to sync with device; possible link problem or link software version mismatch such as hydro rosserial_python with groovy Arduino
```
don't pay attention to it, this is a unsolved package issue from the main developers, but the robot will work without any problem. its recommanded to check th topics to make sure of working fine, too.

---

## How to launch *agribot_imu*

To launch the *agribot_servo* simply run: 

```
$ roslaunch agribot_launch servo.launch
```

Node name : /agribot_imu

Publications: 
 * None

Subscriptions: 
 * servo_pose std_msgs/Int16MultiArray

Services: 
 * None

--- 

**Parameters**
 * None

--- 

### How to Access/Modify Arduino code

To modify the #agribot_servo* code, you should install [Arduino compiler](https://www.arduino.cc) or its plug-in on sublime [Arduin On Sublime](https://packagecontrol.io/packages/Arduino-like%20IDEarduino) and useful tutorial are given in Arduino website as well.

You can access the #agribot_servo* code via link below:
* [*agribot_servo* code](https://github.com/PRBonn/Agribot/tree/master/code/agribot_servo)

---
* [The Main ReadMe](https://github.com/PRBonn/agribot/blob/master/README.md)
* [AgriBot Software](https://github.com/PRBonn/agribot/blob/master/doc/api.md) 

---
### References
* [Stepper motor](https://www.omc-stepperonline.com/closed-loop-stepper-motor/Nema-17-Closed-loop-Geared-Stepper-L60mm-Gear-Raio-511-Encoder-1000CPR.html)
* [Closed loop stepper driver](https://www.omc-stepperonline.com/closed-loop-stepper-driver/closed-loop-stepper-driver-0-70a-24-48vdc-for-nema-17-23-24-stepper-motor-cl57t.html)

--- 
 by: Alireza Ahmadi                                     
 University of Bonn- Robotics & Geodetic Engineering
 
 Alireza.Ahmadi@uni-bonn.de                             
 []()

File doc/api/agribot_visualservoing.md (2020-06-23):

# AgriBot Project (VisualServoing)

---

## About VisualServoing Method
The visualServoing is a technique which uses feedback information extracted from a vision sensor to control the motion of the robot. Its usage in case of AgriBot is to navigate the robot through the crop rows in the field. the main graph of this node is shown. 

<div align="center">
	visualservoing
</div>

In AgriBot navigation strategy, input image will receive from the camera mounted on the front of the robot and as the robot is supposed to work on field expected image is the scene of soil and some crop rows. Hence, features can efficiently be define based on crops and the background will always contain soil and some other plants out of the row, which based on experiments they should be weeds. In figure below the robot and its camera consolation are shown with respect to crop rows in the field.

<div align="center">
	robotinrow
	croprow
	vsout
</div>

---

## About the *agribot_visualservoing* package
In *Agribot_visualservoing* package, a vision sensor as input is used to recognize crop rows, which in the launch file under */launch* directory in the package user change the input source, too. it has access to *agribot_local_planner* and navigation (including *map_server*) to set new goals in */map* frame.

To launch the *agribot_visualservoing* simply run: 
```
$ roslaunch agribot_visualservoing visualservoing.launch
```

**NOTE** to have full functionality, you will need a localization service running to provide position of the robot. In case which you use the robot in the lab, use *mocap* system as localization server.

for more information about *mocap* system refer to this page [Motion Capture](https://github.com/PRBonn/agribot/blob/master/doc/api/mocap.md) 

Node: [/agribot_vs]

Publications: 
 * /cmd_vel [geometry_msgs/Twist]
 * /rosout [rosgraph_msgs/Log]

Subscriptions: 
 * /amcl_pose [unknown type]
 * /odom [unknown type]
 * /usb_cam/image_raw [unknown type]
 * /zed/camera/left/image_raw [sensor_msgs/Image]

Services: 
 * None

--- 

**Parameters**
 * None

--- 
* [The Main ReadMe](https://github.com/PRBonn/agribot/blob/master/README.md)
* [AgriBot Software](https://github.com/PRBonn/agribot/blob/master/doc/api.md) 

--- 
 by: Alireza Ahmadi                                     
 University of Bonn- Robotics & Geodetic Engineering
 
 Alireza.Ahmadi@uni-bonn.de                             
 []()

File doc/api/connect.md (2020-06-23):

# AgriBot Project (Connect to AgirBot)

These instructions are up to guide the user to properly make the connection between a remote PC and AgriBot local processor. Connection could be established by Wifi or Ethernet protocol using ROS platform and [SSH](https://www.hostinger.com/tutorials/ssh-tutorial-how-does-ssh-work#gref) connection.

<!-- <p align="center"><img src="https://cdn.discordapp.com/attachments/205245036084985857/481213000540225550/full_example.gif" /></p> -->

---

## **Necessary Steps to do**:
* [Power up the AgriBot](https://github.com/PRBonn/agribot/blob/master/doc/elec.md#power-up-the-agribot)

--- 

## Table of Contents
- [How to Connect to AgriBot]()
  - [PC Setup](https://github.com/PRBonn/agribot/blob/master/doc/connect.md#pc-setup)
  	- [Wifi Connection](https://github.com/PRBonn/agribot/blob/master/doc/connect.md#wifi-connection)
  	- [Ethernet Connection](https://github.com/PRBonn/agribot/blob/master/doc/connect.md#ethernet-connection)
  - [Bring up](https://github.com/PRBonn/agribot/blob/master/doc/connect.md#bring-up)
  	- [Log into AgriBot PC using HDMI display](https://github.com/PRBonn/agribot/blob/master/doc/connect.md#log-into-agribot-pc-using-hdmi-display)
  	- [Log into AgriBot PC using SSH connection](https://github.com/PRBonn/agribot/blob/master/doc/connect.md#log-into-agribot-pc-using-ssh-connection)
  	- [Using Screen Tool](https://github.com/PRBonn/agribot/blob/master/doc/connect.md#using-screen-tool)
  	- [Run the roscore](https://github.com/PRBonn/agribot/blob/master/doc/connect.md#run-the-roscore)
  	- [Run the Base Controller of AgriBot](https://github.com/PRBonn/agribot/blob/master/doc/connect.md#run-the-base-controller-of-agribot)

---

### PC Setup

**`WARNING`**: The instructions in this part corresponds to the Remote PC (your desktop or laptop PC) which will control AgriBot.

**`NOTE`**: This instruction was tested on Ubuntu 14.04lts with ROS Indigo and Ubuntu 16.04lts with ROS Kinetic.

#### Install Ubuntu and ROS on your PC
- to install Ubuntu you can use following instructions on suggested website [How to install Ubuntu](https://tutorials.ubuntu.com/tutorial/tutorial-install-ubuntu-desktop#0)
- to install ROS use [How to install ROS](http://www.ros.org/install/) 

**`WARNING`** chose correct version of ROS based on version of your Ubuntu.

---

### Network Connection

there are two different methods to access the AgriBot's local processor, Wifi and Ethernet connection. 

**`NOTE`** In case you want to run expensive algorithms like online mapping or recording the data from vision sensors, its recommended to use Ethernet connection as its more reliable and provides more speed. Also, if you want to take the robot outside of the lab you need a local connection through Ethernet switch which is mounted on the robot. 

Here is instructions required to connect to the robot using either Wifi or Ethernet protocols.

for both Wifi and Ethernet connection pay attention to image below, to properly set network properties:

<div align="center">Network-connection</div>

#### Wifi Connection

In case of using  Wifi connection to connect to the robot follow instructions given in this section to connection properly to the robot.

ROS platform requires IP addresses in order to communicate between AgriBot Embedded PC (Raspberry Pi) and the remote PC. The remote PC and AgriBot PC should be connected to the same Wifi router.
Enter the below command on the terminal window of the remote PC to find out the IP address of the remote PC.

```
$ ifconfig
```
Text strings in the rectangle is the IP address of the Remote PC.

<!-- <p align="center"><img src="https://cdn.discordapp.com/attachments/205245036084985857/481213000540225550/full_example.gif" /></p> -->

Enter the below command to open the .bashrc file with nano editor in terminal.

```
$ nano ~/.bashrc
```

<!-- <p align="center"><img src="https://cdn.discordapp.com/attachments/205245036084985857/481213000540225550/full_example.gif" /></p> -->

Press `alt+/` to end line of the file.
Add these two marked lines to modify the address of local host in the `ROS_MASTER_URI` and `ROS_HOSTNAME` with the IP address acquired from the above terminal window. 

<!-- <p align="center"><img src="https://cdn.discordapp.com/attachments/205245036084985857/481213000540225550/full_example.gif" /></p> -->

Then, source the bashrc with below command.

```
$ source ~/.bashrc
```

**`NOTE`**
if you want to run the `ROS Master` on your own system, both IP addresses (`ROS_MASTER_URI` and `ROS_HOSTNAME`) should be set equal to your IP address, and some changes should be done AgriBot system which are explained in [Changing Master PC]().

#### Ethernet Connection

In case that you want to connect to the AgriBot through Ethernet protocol, you need to make the connection through Ethernet switch mounted on the robot. 
- the IP address should be set manually in you system in range of 196.168.0.x like image below:

<!-- <p align="center"><img src="https://cdn.discordapp.com/attachments/205245036084985857/481213000540225550/full_example.gif" /></p> -->

After establishing the connection, please follow below instructions:

- fist test the connection with entering:

```
$ ifconfig
```
make sure specified IP address is shown under title of Ethernet connection.

Enter the below command to open the .bashrc file with nano editor in terminal.

```
$ nano ~/.bashrc
```

<!-- <p align="center"><img src="https://cdn.discordapp.com/attachments/205245036084985857/481213000540225550/full_example.gif" /></p> -->

Press `alt+/` to end line of the file.
Add these two marked lines to modify the address of local host in the `ROS_MASTER_URI` and `ROS_HOSTNAME` with the IP address acquired from the above terminal window. 

<!-- <p align="center"><img src="https://cdn.discordapp.com/attachments/205245036084985857/481213000540225550/full_example.gif" /></p> -->

Then, source the bashrc with below command.

```
$ source ~/.bashrc
```

---

### Bring up

**`WARNING`** 
- This instruction is intended to be run on the remote PC. If you are following above instruction, please do run the `roscore` command on AgriBot PC or just launch desired launch file.
- Make sure that IP address on each device is set correctly.

##### Log into AgriBot PC using HDMI display

**NOTE**: The terminal application can be found with the Ubuntu search icon on the top left corner of the screen. Shortcut key for terminal is Ctrl-Alt-T.

##### Log into AgriBot PC using SSH connection

**NOTE**: The terminal application can be found with the Ubuntu search icon on the top left corner of the screen. Shortcut key for terminal is Ctrl-Alt-T.

##### Using Screen Tool

In case you want to disconnect your system or shutdown the SSH connection and have the nodes running on the AgriBot local processor use screen.

Screen is a console application that allows you to use multiple terminal sessions within one window. The program operates within a shell session and acts as a container and manager for other terminal sessions, similar to how a window manager manages windows.[reference](https://www.digitalocean.com/community/tutorials/how-to-install-and-use-screen-on-an-ubuntu-cloud-server) 

**How to install screen**

Use “apt-get” to install on Ubuntu:
```
sudo apt-get update
sudo apt-get install screen
```
Run the application on terminal:

```
screen
```
**`NOTE`** to use the screen tool to run the nodes on AgriBot, just run the command screen before running SSH commands on your own PC. 

image below is showing required steps:

<!-- <p align="center"><img src="https://cdn.discordapp.com/attachments/205245036084985857/481213000540225550/full_example.gif" /></p> -->

###### Run the roscore

In case you need to debug or develop a code, its better to run the roscore separately to have it always running. Otherwise is each time you want to run your program (using launch files) you will need to shutdown all nodes like simulators  or dependent nodes which you had ran before, because they won't recognize new roscore.

```
$ roscore
```
**`NOTE`** if you just need to run the robot to record data or have a performance, its not necessary to run the roscore separately.
###### Run the Base Controller of AgriBot

following command will run all required nodes to record data and drive the robot. 

to run this command in case which you have ran roscore before, open another terminal tab with `<Shift+Ctrl+T>` and follow instruction in part [SSH](https://github.com/PRBonn/agribot/blob/master/doc/connect.md#log-into-agribot-pc-using-ssh-connection).

In the new tab enter command below:

```
$ roslaunch agribot_launch base.launch
```

If every this is going well and all sensors and actuators are connected and connection are flawless, the terminal will represent below messages.

**`NOTE`** More information about Nodes and launch files are given in [AgriBot Software](https://github.com/PRBonn/agribot/blob/master/doc/api.md) section. 

**`NOTE`** if connection between Raspberry Pi and motor drives (from motors) cant be established correctly (in any case of faults in connection or power or etc) relays on the robot will begin to switch on and off and buzzer will make alarm of a continuous sound.

---
* [The Main ReadMe](https://github.com/PRBonn/agribot/blob/master/README.md)

--- 
 by: Alireza Ahmadi                                     
 University of Bonn- Robotics & Geodetic Engineering
 
 Alireza.Ahmadi@uni-bonn.de                             
 []()

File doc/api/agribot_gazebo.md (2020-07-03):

# AgriBot Project (Gazebo)

---

### About the *agribot_gazebo* package

this package contains the models of plants and the world which is designed to robot be spawned into it and it looks like a small farm. it has a launch file to spawn the robot and initialize the world. 

YouTube: [Agribot Simulation Demo](https://youtu.be/aYkh9gSbTDI)

**`NOTE`** make sure you have updated your gazebo and you have installed gazebo-ros and controller-manager packages before running the simulation. used these commands to install them properly.

```
sudo apt-get update
sudo apt-get install ros-<DISTRO_OF_YOUR_ROS>-gazebo-ros*
sudo apt-get install ros-<DISTRO_OF_YOUR_ROS>-controller-manager
```
the created simulation provides IMU, GPS, Camera and wheel Odometry on the same topics as actual robot which gives this opportunity to run same codes on the simulation as the actual robot without any changes.
The image below shows the final version of simulation area and a robot spawned into environment.

<div align="center">gazebo-crop</div>

## Adding Plant modes to Gazebo

add plant models to gazebo models using command below, first navigate to agribot/agribot_gazebo: 

```
cd ~/catkin_ws/src/agribot/agribot_gazebo/models
```

then copy models to gazebo models folder by:

in z-shell
```
sudo mv plant_/* ~/.gazebo/models/
```
or in  shell
```
sudo mv plant_* ~/.gazebo/models/
```
now you should be able to see plant models in gazebo models lists according to image below

<div align="center">gazebo-crop</div>

To launch the `agribot_gazebo` simply run: 
```
$ roslaunch agribot_gazebo agribot_sb_farm.launch
```

**`NOTE`** to find more information about gazebo environment and how to define robots in this simulator please visit [Gazebo website](http://gazebosim.org/tutorials/?tut=ros_urdf) 

the launch file is taking the configuration of an empty world which is a default layer in gazebo environment and then makes the farm model on top of it. also, with given coordinates spawns the robot too. 

**`NOTE`** the description of the robot is loading from `agribot_control` package which contains the controllers and main description of the robot in format of URDF and XACRO files. for more information visit [agribot_control](https://github.com/PRBonn/agribot/blob/master/doc/api/agribot_control.md)

```xml
<?xml version="1.0"?>
<launch>

  <!-- these are the arguments you can pass this launch file, for example paused:=true -->
  <arg name="paused" default="false"/>
  <arg name="use_sim_time" default="true"/>
  <arg name="gui" default="true"/>
  <arg name="headless" default="false"/>
  <arg name="debug" default="false"/>

  <!-- We resume the logic in empty_world.launch, changing only the name of the world to be launched -->
  <include file="$(find gazebo_ros)/launch/empty_world.launch">
    <arg name="world_name" value="$(find agribot_gazebo)/worlds/farm.world"/>
    <arg name="debug" value="$(arg debug)" />
    <arg name="gui" value="$(arg gui)" />
    <arg name="paused" value="$(arg paused)"/>
    <arg name="use_sim_time" value="$(arg use_sim_time)"/>
    <arg name="headless" value="$(arg headless)"/>
  </include>

  <!-- Spawn a robot into Gazebo -->
  <param name="robot_description" command="$(find xacro)/xacro.py '$(find agribot_control)/urdf/agribot.xacro'"/>

  <node name="agribot_spawn" pkg="gazebo_ros" type="spawn_model" output="screen" respawn="false"
   args="-x 6 -y -1 -z 1.13 -Y 1.57079 -urdf -param robot_description -model agribot" />

  <!-- ros_control pioneer launch file -->
<!--   <include file="$(find agribot_control)/launch/agribot_control.launch" />
 -->
</launch>

```

--- 
* [The Main ReadMe](https://github.com/PRBonn/agribot/blob/master/README.md)
* [AgriBot Software](https://github.com/PRBonn/agribot/blob/master/doc/api.md) 

--- 
 by: Alireza Ahmadi                                     
 University of Bonn- Robotics & Geodetic Engineering
 
 Alireza.Ahmadi@uni-bonn.de                             
 []()

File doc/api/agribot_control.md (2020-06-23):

# AgriBot Project (agribot_control)

---

## About the *agribot_control* package
This package contains the description of the robot in URDF and XACRO forms along with gazebo plug-ins to actuate the robot in the simulation environment. The initial URDF is extracted from SolidWorks software, in the mechanical design section. Also it contains all the required information about the TF and different coordinate systems used in the robot (all are defined same as the actual robot).

this package comes with some launch files which the most important one is the *agribot_rviz.launch* which loads the robot into parameter-server and then the RVIZ simulator can access to the robot description values and show the robot.

<div align="center">
	rvizagribot
</div>

To launch the agribot_control simply run: 
```
$ roslaunch agribot_control agribot_rviz.launch
```

The other launch file is a controller manager which runs with gazebo and tries to publish and control the status of all active joints loaded into gazebo in run-time. to run this controller first launch [agribot_gazebo](https://github.com/PRBonn/agribot/blob/master/doc/api/agribot_gazebo.md) and then used command below:

```
$ roslaunch agribot_control agribot_control.launch
```

--- 
* [The Main ReadMe](https://github.com/PRBonn/agribot/blob/master/README.md)
* [AgriBot Softwarea](https://github.com/PRBonn/agribot/blob/master/doc/api.md) 

--- 
 by: Alireza Ahmadi                                     
 University of Bonn- Robotics & Geodetic Engineering
 
 Alireza.Ahmadi@uni-bonn.de                             
 []()

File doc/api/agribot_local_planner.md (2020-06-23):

# AgriBot Project (Local Planner)

---

AgriBot-Local Planner Package Demo (https://www.youtube.com/watch?time_continue=1&v=xCAXH3JesxI "AgriBot-Local Planner Package Demo")

### About the *agribot_local_planner* package
The process of determining speed and steering of the robot at each epoch of time in order to navigate the robot through a given trajectory is called trajectory or path tracking. A path consists of a set of consecutive poses in a planned way. As mentioned earlier, global planner generates the main path and local planner performs some actions to drive the robot to the goals or points specified on trajectory. 

In the ROS platform, there are some implementations of local planner package which based on our experiments neither of them was able to control AgriBot optimally. Therefore, we implemented our own local planner which breaks down the path published by the global planner and utilizes DynamicWindowApproach (DWA)along with PID controller to approach the closest targets and keeps doing this until robot reaches to the final goal. 

<div align="center">
	navgraph
</div>

In shown image, a set of temporal targets distributed between robots current pose and final goal are shown. Each temporal target has one position and one specific orientation shown with green arrows. The orientation is derived from simple triangulation between two nearest poses generated by global planner (they don't have specific orientation) and selection of poses to set as a target is done based on DWA method. 

As Robot moves on the track the odometric errors can disturb the traversing path from the planned path, in such situations both local and global planner should be able to update the path to handle unplanned positional and orientation deviations, hence, both planners are able to updating their outputs based on robots pose and velocities and the estimated errors.

When a temporary goal gets selected by the DWA method, both linear and orientation wise errors get computed. The linear error is the distance between current position of the robot to the selected temporary goal. Also, the orientation error defines to cover the angle between the current robots heading and the line drawn from the center of the robot to the next goal. Then, a PID controller aims to minimize the orientation error. Also, another PID instance as a linear controller is used to get the robot closer to the goal to minimize the distance error. 

## How to launch *agribot_local_planner*
As local planner is an implementation of a plug-in dependent of [*move_base*](http://wiki.ros.org/move_base) package, it will show up in the launch file, where we launch the *move_base* core in the [*agribot_navigation*](https://github.com/PRBonn/agribot/blob/master/doc/api/agribot_navigation.md)package.

```xml
<?xml version="1.0"?>
<launch>
  <node pkg="move_base" type="move_base" respawn="false" name="move_base"  output="screen">
    <rosparam file="$(find agribot_navigation)/params/costmap_common_params.yaml" command="load" ns="global_costmap" />
    <rosparam file="$(find agribot_navigation)/params/costmap_common_params.yaml" command="load" ns="local_costmap" />
    <rosparam file="$(find agribot_navigation)/params/local_costmap_params.yaml" command="load" />
    <rosparam file="$(find agribot_navigation)/params/global_costmap_params.yaml" command="load" />
    <rosparam file="$(find agribot_navigation)/params/base_local_planner_params.yaml" command="load" />
    <rosparam file="$(find agribot_navigation)/params/move_base_params.yaml" command="load" />
    <rosparam file="$(find agribot_navigation)/params/costmap.yaml" command="load" ns="/costmap_node/costmap" />
    <param name="base_global_planner" type="string" value="navfn/NavfnROS"/>
    <!--param name="base_global_planner" value="agribot_global_planner/AgribotGlobalPlanner"/-->
    <param name="base_local_planner" value="agribot_local_planner/AgribotLocalPlanner"/>
    <remap from="sensor_pose_odo" to="/mocap_odom" />
    <remap from="cmd_vel" to="/cmd_vel" />
    <remap from="map" to="/map" />
  </node>
  <!--node name="rqt_reconfigure" pkg="rqt_reconfigure" type="rqt_reconfigure" output="screen"/-->
  <!--node name="rqt_plot" pkg="rqt_plot" type="rqt_plot" output="screen"/-->
</launch>
```

* Also it uses [*Dynamic_reconfigure*](http://wiki.ros.org/dynamic_reconfigure) which, provides access to defined parameters at the run-time. 

--- 
* [The Main ReadMe](https://github.com/PRBonn/agribot/blob/master/README.md)
* [AgriBot Software](https://github.com/PRBonn/agribot/blob/master/doc/api.md)

--- 
 by: Alireza Ahmadi                                     
 University of Bonn- Robotics & Geodetic Engineering
 
 Alireza.Ahmadi@uni-bonn.de                             
 []()

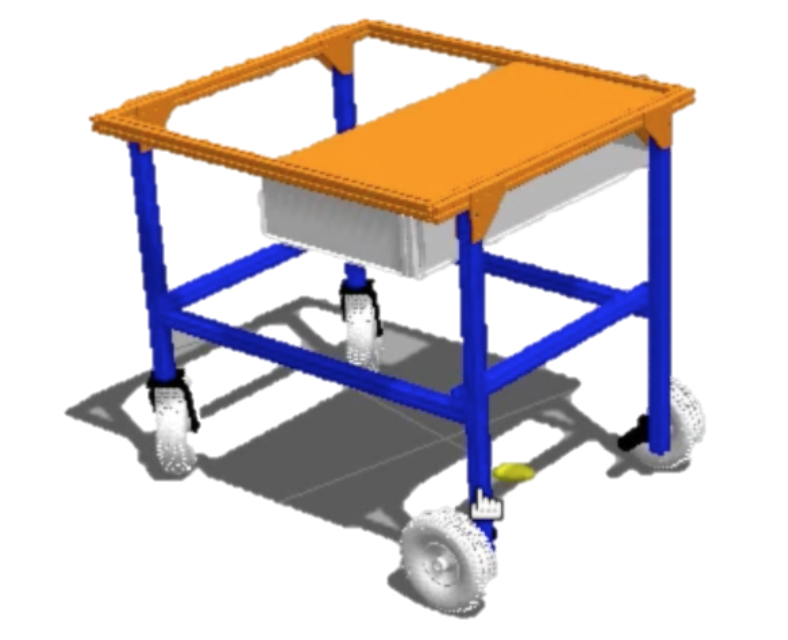
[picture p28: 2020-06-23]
doc/images/gazebo.png

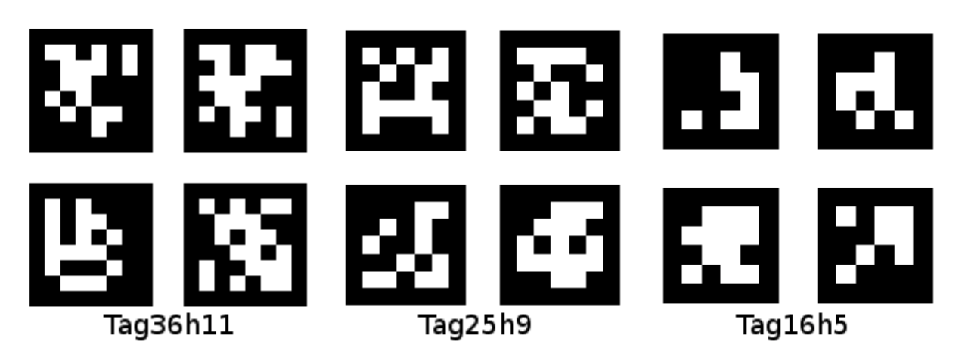
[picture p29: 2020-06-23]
doc/images/apriltags.png

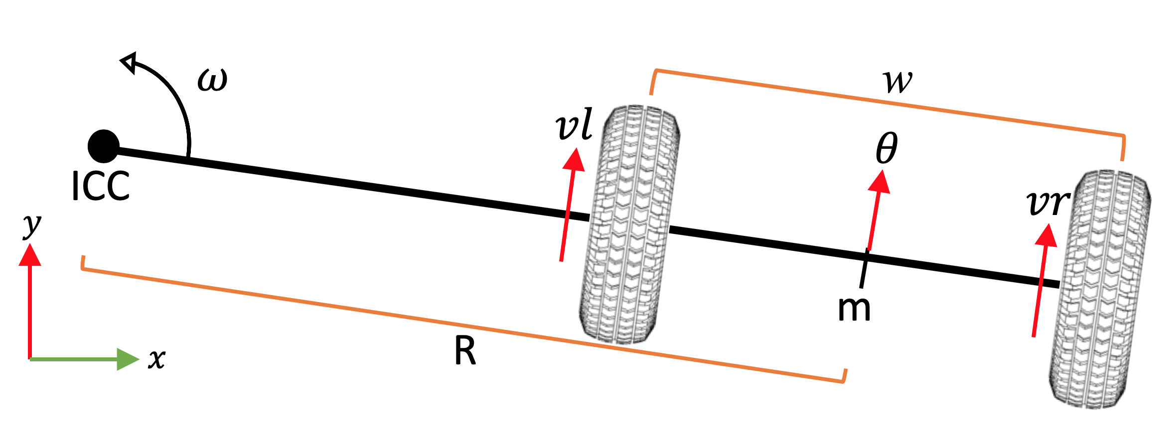
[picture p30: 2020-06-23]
doc/images/diff.png

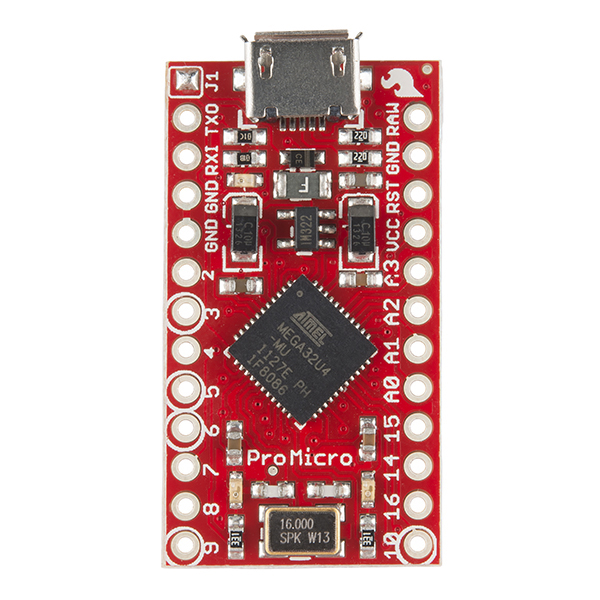
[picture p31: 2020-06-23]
doc/images/promicro.png

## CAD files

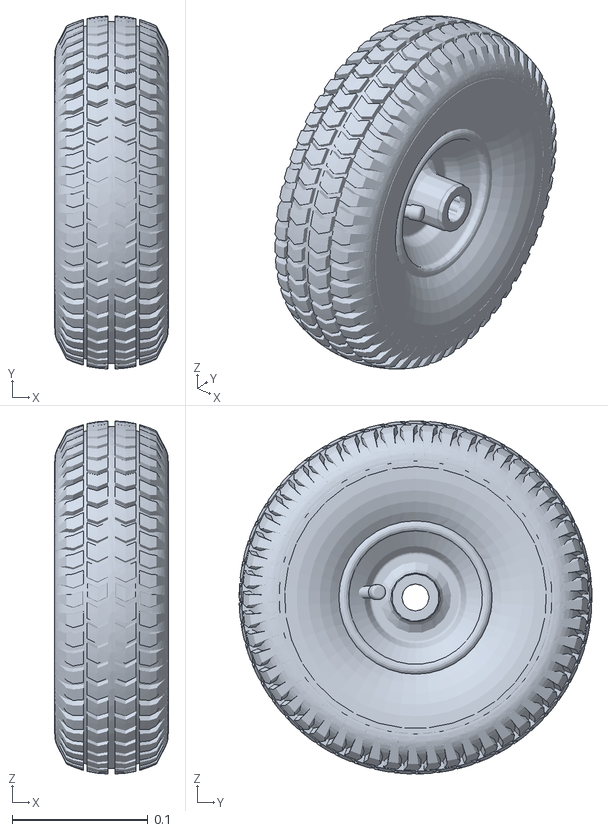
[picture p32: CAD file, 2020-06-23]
agribot_control/meshes/front_w_r.STL
0.084 x 0.26 x 0.26

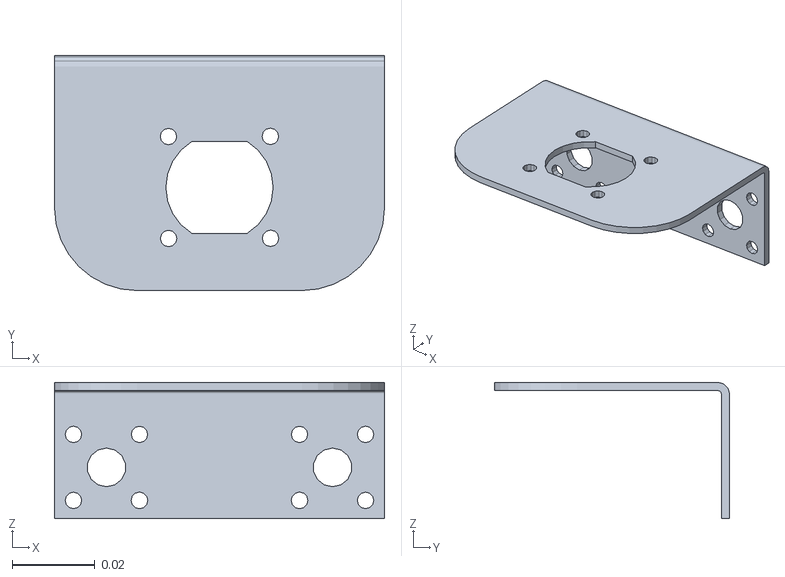
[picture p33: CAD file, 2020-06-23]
agribot_description/meshes/right_front_motor.STL
0.08 x 0.057 x 0.033

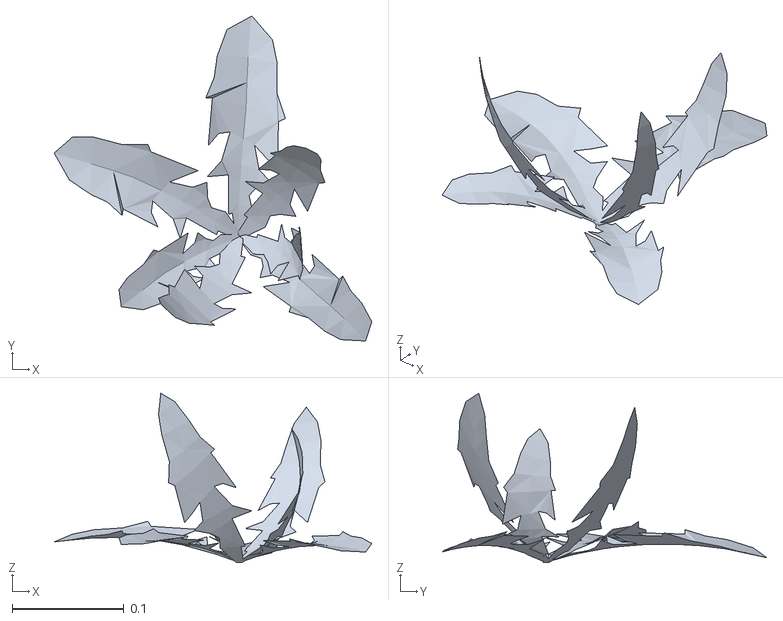
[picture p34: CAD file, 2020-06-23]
agribot_gazebo/models/big_plant/mesh/big_plant.stl
0.285 x 0.291 x 0.152

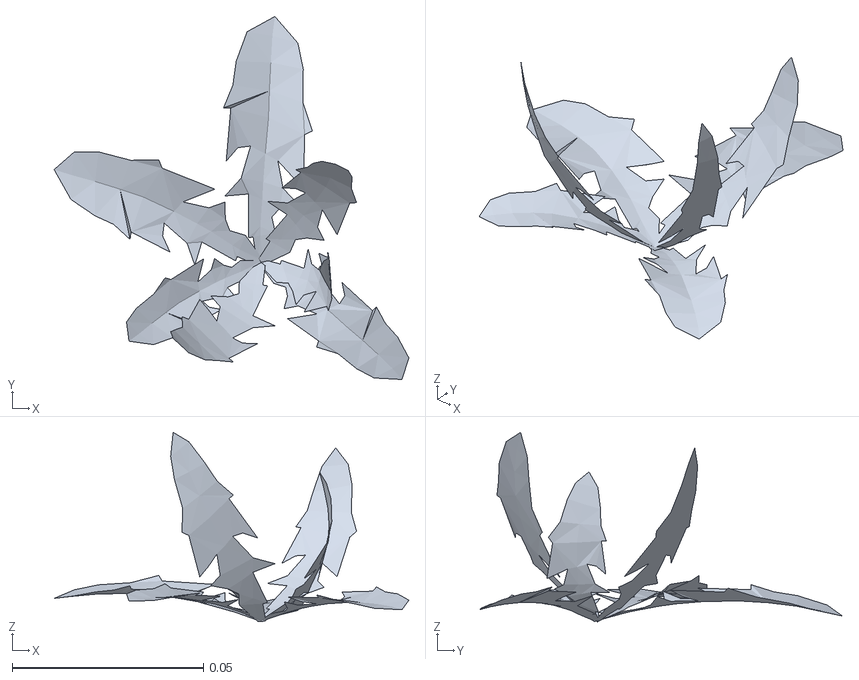
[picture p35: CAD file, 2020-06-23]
agribot_gazebo/models/small_plant/mesh/small_plant.stl
0.0928 x 0.0949 x 0.0495

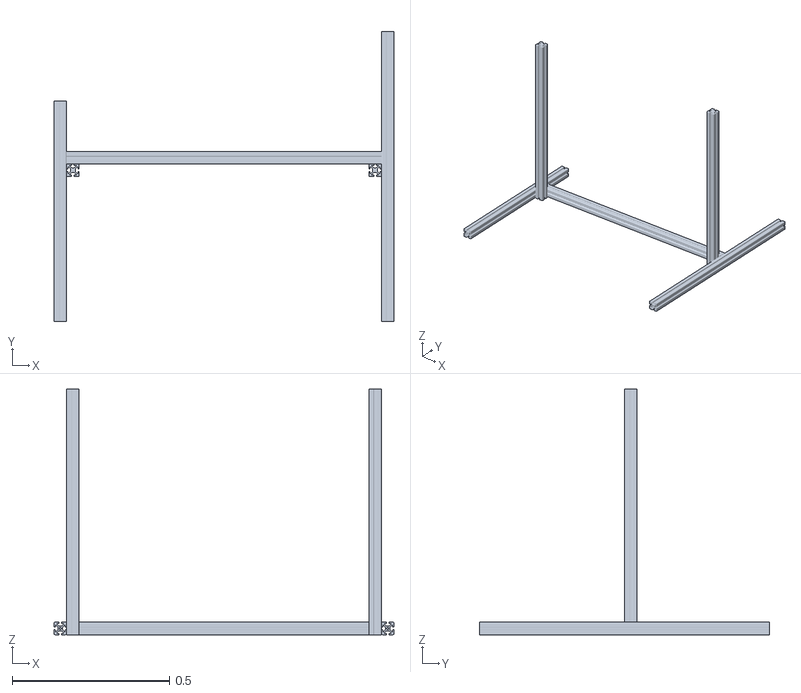
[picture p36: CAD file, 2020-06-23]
agribot_control/meshes/right_leg.STL
1.08 x 0.92 x 0.78

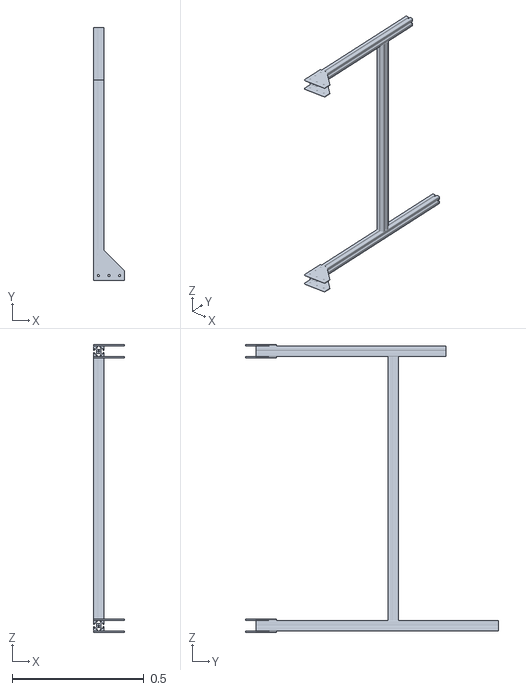
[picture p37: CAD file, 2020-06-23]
agribot_description/meshes/right_leg.STL
0.118 x 0.96 x 1.09

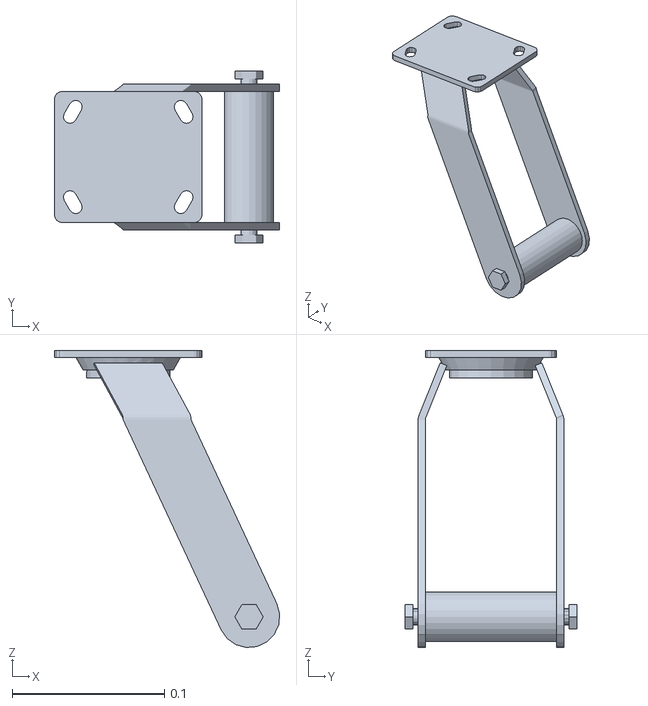
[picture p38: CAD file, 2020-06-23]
agribot_control/meshes/back_c_l.STL
0.148 x 0.113 x 0.195

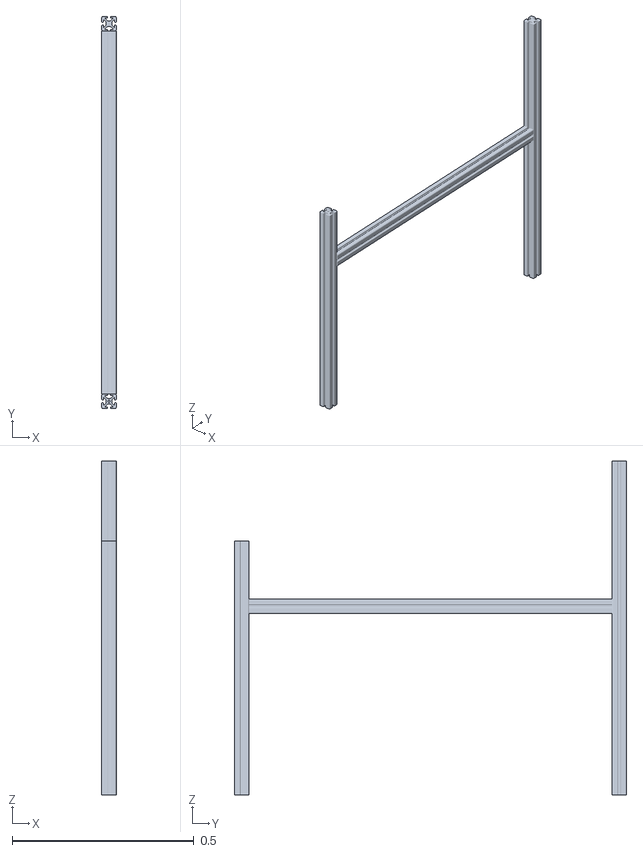
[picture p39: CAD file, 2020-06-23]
agribot_control/meshes/left_leg.STL
0.04 x 1.08 x 0.92

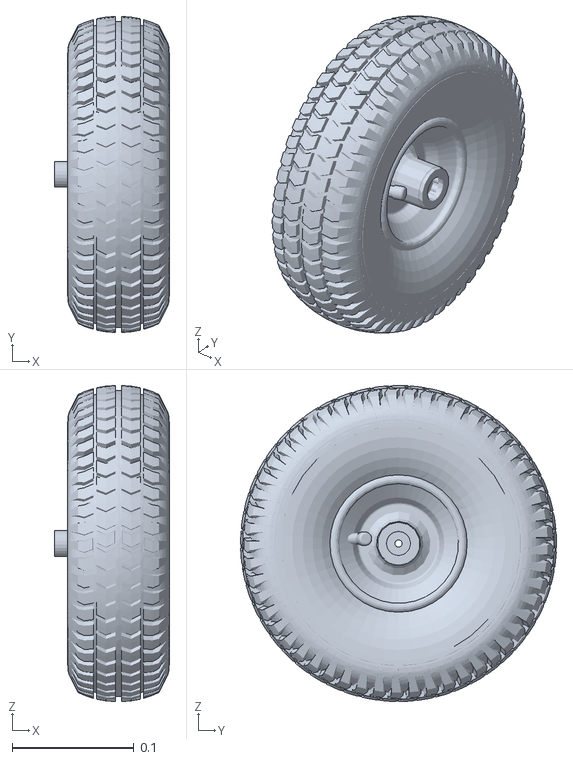
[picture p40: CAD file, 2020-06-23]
agribot_description/meshes/left_fron_wheel.STL
0.0947 x 0.26 x 0.26

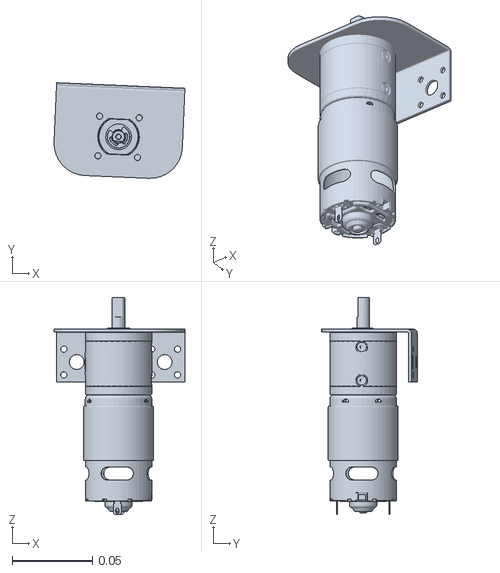
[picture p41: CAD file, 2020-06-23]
agribot_control/meshes/front_m_l.STL
0.0815 x 0.0596 x 0.135

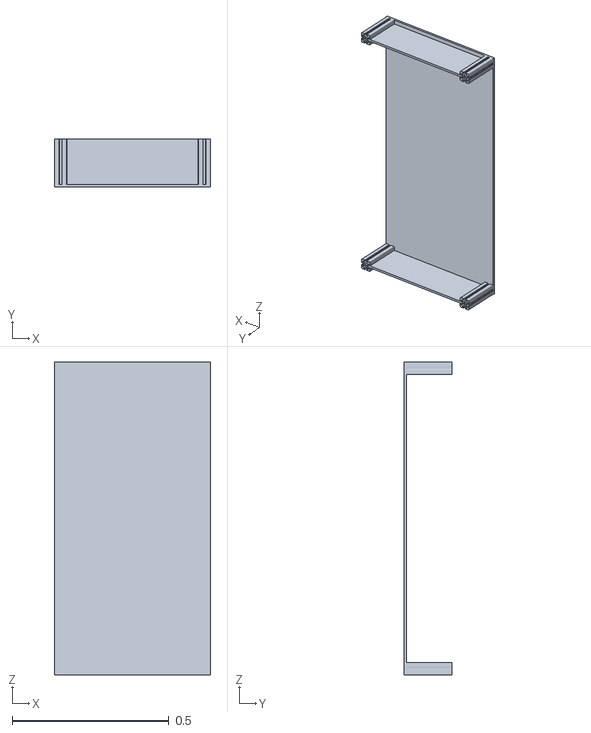
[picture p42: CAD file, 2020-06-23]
agribot_control/meshes/sensor_box.STL
0.5 x 0.153 x 1.00

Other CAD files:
agribot_description/meshes/right_back_u.STL
agribot_control/meshes/back_w_l.STL
agribot_description/meshes/right_front_wheel.STL
agribot_control/meshes/front_w_l.STL
agribot_description/meshes/left_back_u.STL
agribot_description/meshes/left_leg.STL
agribot_description/meshes/left_back_wheel.STL
agribot_control/meshes/back_c_r.STL
agribot_control/meshes/back_w_r.STL
agribot_control/meshes/base_link.STL
agribot_control/meshes/front_m_r.STL
agribot_description/meshes/ZED.stl
agribot_description/meshes/base_link.STL
agribot_description/meshes/left_fron_motor.STL
agribot_description/meshes/right_back_wheel.STL

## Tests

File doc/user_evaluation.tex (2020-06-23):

\documentclass[10pt,a4paper]{article}
\usepackage{geometry}
\usepackage{layaureo}% loads package geometry
\usepackage[legalpaper, landscape, margin=2in]{geometry}
\usepackage[margin=1in]{geometry}
\usepackage[latin1]{inputenc}
\usepackage{amsmath}
\usepackage{amsfonts}
\usepackage{amssymb}
\usepackage{graphicx}
\usepackage{enumitem,amssymb}
\newlist{todolist}{itemize}{2}
\setlist[todolist]{label=$\square$}
\title{AgriBot : User Evaluation}
\author{Evaluator's name}
\begin{document}
\maketitle

\section{Goal}

The goal of this exercise is to evaluate the user experience while operating
the AgriBot as a data recording platform. To perform the evaluation, the user is
first requested to go through the documentation and then execute a series of tasks. The developers will be present during the evaluation and provide assistance only if
requested by the user. The estimated time required to perform the evaluation is as follows:
\begin{itemize}
	\item Reading the documentaion : 20 Mins
	\item Executing the list of tasks : 30 Mins
	\item Provide feedback: 10 mins
\end{itemize}

\section{Task description and evaluation}

The tasks are designed to evaluate whether the readiness of the platform for a new user to operate and record data from its on-board sensors. The user is requested to go through the task list sequentially and tick the appropriate check box. Please tick on Yes only if you were able to complete the task without any assistance from the developers.   

\begin{enumerate}
	\item \textbf{Task 1}: Turn on the robot.
		\begin{todolist}
			\item Yes
			\item No
		\end{todolist}

	\item \textbf{Task 2}: Connect your laptop to the AgriBot using the Ethernet setup.
		\begin{todolist}
			\item Yes
			\item No
		\end{todolist}

	\item \textbf{Task 3}: Control the AgriBot using the joystick. Try to drive in different modes and perform simple maneuvers such following a straight line or take a turn.
		\begin{todolist}
			\item Yes
			\item No
		\end{todolist}
				
	\item \textbf{Task 4}: Take the AgriBot outside the lab and record data.
		\begin{todolist}
			\item Yes
			\item No
		\end{todolist}
		
	\item \textbf{Task 5}: Bring the AgriBot back to the lab, shut it down and
		charge the batteries. 
		\begin{todolist}
			\item Yes
			\item No
		\end{todolist}
		
\end{enumerate}

\section{Feedback}

\begin{enumerate}
	\item Which tasks lacked sufficient/clear documentation? What additional documentation is required?  \\ 
		\framebox(400,80){} 
		
	\item What additional features would you like in order to make the whole process
	of data collection easier?  \\ 
		\framebox(400,80){}
		
	\item How easy/difficult was it to control the AgriBot using the joystick? What additional controls/changes would you recommend? \\	
		\framebox(400,80){}				
	
	\item What things would you like to be improved about the AgriBot as a whole?\\	
		\framebox(400,80){}				
\end{enumerate}

\end{document}

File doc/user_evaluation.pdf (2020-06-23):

# AgriBot : User Evaluation

Evaluator’s name

February 22, 2019

## 1 Goal

The goal of this exercise is to evaluate the user experience while operating the AgriBot as a data recording platform. To perform the evaluation, the user is first requested to go through the documentation and then execute a series of tasks. The developers will be present during the evaluation and provide assistance only if requested by the user. The estimated time required to perform the evaluation is as follows:

- Reading the documentaion : 20 Mins
- Executing the list of tasks : 30 Mins
- Provide feedback: 10 mins

## 2 Task description and evaluation

The tasks are designed to evaluate whether the readiness of the platform for a new user to operate and record data from its on-board sensors. The user is requested to go through the task list sequentially and tick the appropriate check box. Please tick on Yes only if you were able to complete the task without any assistance from the developers.

1. Task 1: Turn on the robot.

Yes

No

2. Task 2: Connect your laptop to the AgriBot using the Ethernet setup.

Yes

No

3. Task 3: Control the AgriBot using the joystick. Try to drive in different modes and perform simple maneuvers such following a straight line or take a turn.

Yes

No

4. Task 4: Take the AgriBot outside the lab and record data.

Yes

1

No

5. Task 5: Bring the AgriBot back to the lab, shut it down and charge the batteries.

Yes

No

## 3 Feedback

1. Which tasks lacked sufficient/clear documentation? What additional documentation is required?
2. What additional features would you like in order to make the whole process of data collection easier?
3. How easy/difficult was it to control the AgriBot using the joystick? What additional controls/changes would you recommend?
4. What things would you like to be improved about the AgriBot as a whole?

2

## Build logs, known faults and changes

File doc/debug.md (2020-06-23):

# AgriBot - Agricultural Mobile Robot Platform

---

## Table of Contents
- [Debug The Electrical Connections](https://github.com/PRBonn/agribot/blob/master/doc/dedug.md#debug-the-electrical-connections)
- [Debug The Network Connection](https://github.com/PRBonn/agribot/blob/master/doc/dedug.md#debug-the-network-connection)
- [Debug The Mechanical Parts](https://github.com/PRBonn/agribot/blob/master/doc/debug.md#debug-the-mechanical-parts)

---

### Debug The Electrical Connections

The potential problems in electrical connections could be the I/O pins which are connecting different devices to each other. for example the relays, drivers, and embedded controller on IMU and servo controller part. 
to debug them the best way is to first read the explanations provided in the related section and then based on the maps of I/O pins and find the problem.

* whenever its required to do some electrical debug, please make sure that the power is off.
* Also, by checking the data-sheets of different components you can find out more about the type of connection.

**`NOTE`** further information about electrical connections of each part (like servos, IMU,..) is given in the related section under the [AgriBot Software](https://github.com/PRBonn/agribot/blob/master/doc/api.md).

---

### Debug The Network Connection

In case of having any issue with Network and making connection to the Agribot please first, read the [How to Connect to AgriBot](https://github.com/PRBonn/agribot/blob/master/doc/recorddata.md#how-to-connect-to-agribot), and in case which you couldn't find or solve the problem, follow the instructions below:

1. make sure all setting are set according to the [How to Connect to AgriBot](https://github.com/PRBonn/agribot/blob/master/doc/recorddata.md#how-to-connect-to-agribot)

* In case of having problem with Ethernet connection: 
2. check the cable of Ethernet connection from Raspberry pi to the switch mounted on the robot.
3. check the Ethernet cable which connects your PC to the switch.
4. reset the Ethernet switch on the robot. 
5. create a static IP manually for your PC in range of IP: 192.168.0.x with Net-mask: 24
6. check your IP address by using 

```
$ ifconfig
```

7. On the Remote PC use command below to make sure raspberry pi in reachable in the network.

```
$ ping 192.168.0.100 
```
if IP was reachable then problem should be solved.

* In case of having problem with Wifi connection: 
2. reset the Wifi router.
3. create a static IP manually for your PC in range of IP: 131.220.233.x with Net-mask: 24
4. check your IP address by using 

```
$ ifconfig
```

5. On the Remote PC use command below to make sure raspberry pi in reachable in the network.

```
$ ping 131.220.233.190 
```
if IP was reachable then problem should be solved.

---

### Debug The Mechanical Parts

As all the mechanical parts are attached together by screws and nuts, its recommended to check the connections and tight them up sometimes, specially, in time of taking the robot to the fields or doing experiments with long run. 

The most important mechanical parts and connection which can affect the performances is listed here:

1. Main connection of both legs in front and the back of the robot. (please take care of the dimensions when you tight screws, use a meter to measure the distance between legs and match them to specification shown in [Mechanical Design](https://github.com/PRBonn/agribot/blob/master/doc/mec.md)), also check the screws on the  profiles which are used to fix legs together.  

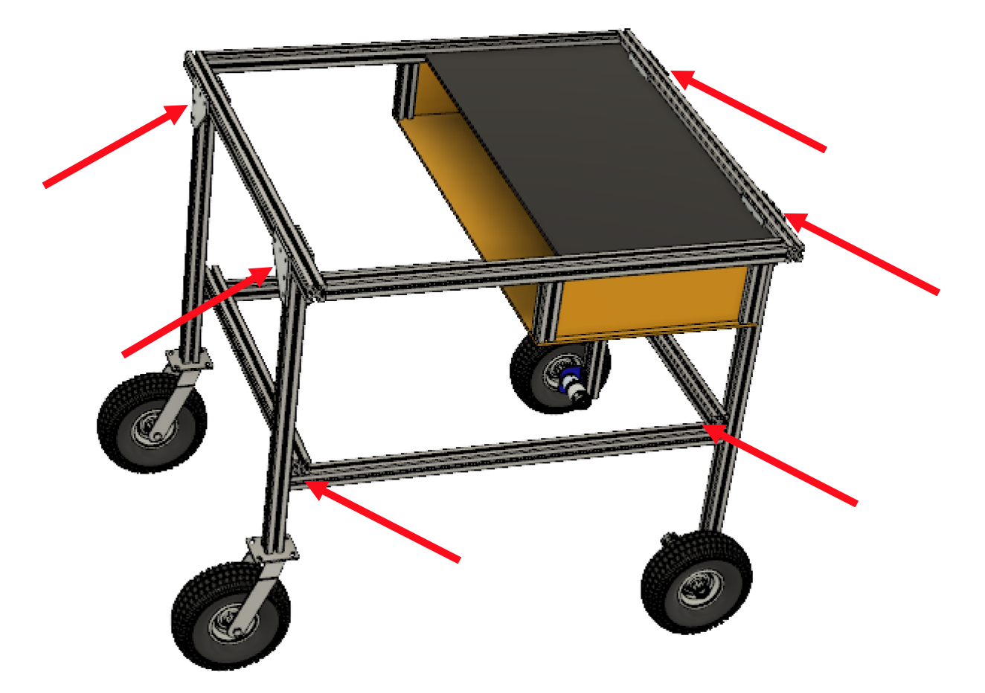
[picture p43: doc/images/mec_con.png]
mec_con


2. Connection of servo motors at rear axes (where the shaft of caster wheel is connected to the shaft of servo motor using a coupler). check all the screws on the coupler part.

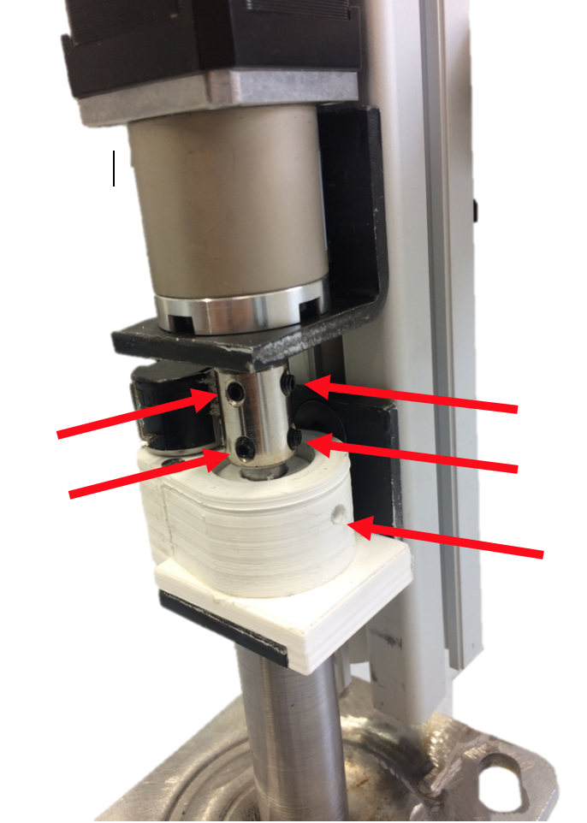
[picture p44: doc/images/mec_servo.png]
mec_servo


3. Connection of front wheels to the motors and the connection of motors to the U-shape hinge of front wheels.

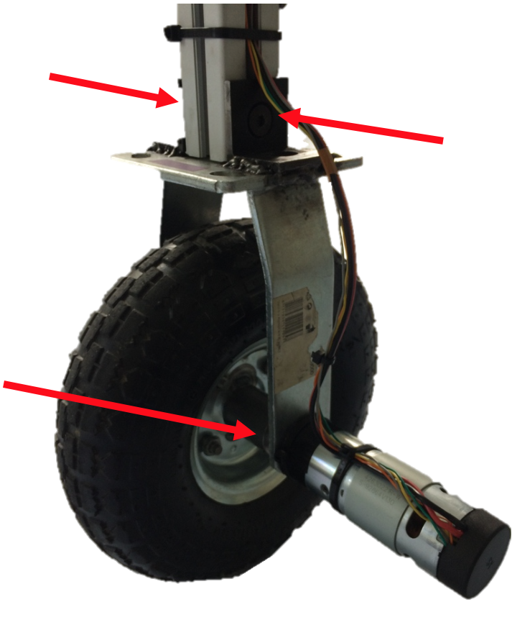
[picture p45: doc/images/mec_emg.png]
mec_emg


---

[The Main ReadMe](https://github.com/PRBonn/agribot/blob/master/README.md)

*Section*:
- [Mechanical Design](https://github.com/PRBonn/agribot/blob/master/doc/mec.md)
- [Electrical  Design](https://github.com/PRBonn/agribot/blob/master/doc/elec.md)
- [AgriBot Software](https://github.com/PRBonn/agribot/blob/master/doc/api.md) 
- [Easy Bring up & Record Data](https://github.com/PRBonn/agribot/blob/master/doc/recorddata.md) 

--- 
 by: [Alireza Ahmadi](https://github.com/alirezaahmadi)                                     
 University of Bonn- Robotics & Geodetic Engineering

 Alireza.Ahmadi@uni-bonn.de

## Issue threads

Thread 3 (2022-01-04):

ROS2?

samuk, 2022-01-04:
I'm interested in trying https://github.com/PRBonn/agribot/blob/master/doc/api/agribot_visualservoing.md

Under ROS2 on this hardware: https://github.com/samuk/earth_rover_localization#bom-mostly-open-hardware

You planning to upgrade to ROS2?

alirezaahmadi, 2022-01-05:
We will release a multi-crop row version (python version) but unfortunately there is no plan for taking it to ROS2

samuk, 2022-01-05:
Thanks, I'll investigate if it might be possible to integrate the visual servoing python version into https://vox-nav.readthedocs.io/en/latest/configuration/index.html as one of the navigation strategies.

samuk, 2022-01-09:
Seems VOX is not the right way to approach this in ROS2.

Do you have a rough estimate of when the Python version will be available? Or is there a /dev repo I could take a look at?

Discussing it here: https://discourse.ros.org/t/navigation-for-precision-farming-in-open-fields/15138/13 if you're interested in contributing to that conversation.

alirezaahmadi, 2022-01-09:
Hi,

The python version is almost ready but needs to be cleaned up and get ready for getting public, this must happen in a few weeks I would say because I am pretty busy right now.
Can I ask what is the project your working on?? Maybe I can contribute!!

Best
Alireza Ahmadi
Research Assistant and Doctoral student
Department of Agricultural Robotics and Engineering
PhenoRob (Cluster of Excellence)
University of Bonn
Nussallee 5, 53115 Bonn, Germany
Tel: +49-(0)288-73-4602
Email: ***@***.***

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

samuk, 2022-01-09:
Great, thanks!

It's not a 'proper' agbot, just a toy really: https://github.com/samuk/Sawppy_Rover/blob/main/modifications/Ag/readme.md

I hope that in time it could develop into something practical & useful.

Closed 2022-01-05.

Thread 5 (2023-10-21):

Video capture

ismailorhanbas, 2023-10-21:
Hi i want to try your visiual servoing code on simulation but i have problem with camera umd launch because of usb cam package. I couldt properly change launch file, by just changing video device video2 to agribot/front cam or something, can you give me a guidience to use your visiual servoing package in a simulation.

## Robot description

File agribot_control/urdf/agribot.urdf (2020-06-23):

<?xml version="1.0"?>
<robot name="agribot">
   <link name="base_link">
    <inertial>
      <origin xyz="0.111078485559937 0.000705580494722497 -0.00585333353825024" rpy="0 0 0" />
      <mass value="7.9509272490726" />
      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
    </inertial>
    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
  </link>
  <link name="left_leg">
    <inertial>
      <origin xyz="-1.66533453693773E-16 -0.477061379270826 0.150081974979978" rpy="0 0 0" />
      <mass value="2.41451388541046" />
      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
    </inertial>
    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
  </link>
  <joint name="left_leg_joint" type="fixed">
    <origin xyz="0.507757199999999 0.37 -0.3288" rpy="3.14159265358979 0 1.5707963267949" />
    <parent link="base_link" />
    <child link="left_leg" />
    <axis xyz="0 0 0" />
  </joint>
  <link name="right_leg">
    <inertial>
      <origin xyz="0.50695885654552 -0.0152487488854501 -0.146120125360058" rpy="0 0 0" />
      <mass value="3.84570821080266" />
      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
    </inertial>
    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
  </link>
  <joint name="right_leg_joint" type="fixed">
    <origin xyz="-0.492242799999999 -0.0851999999999998 -0.504" rpy="-1.5707963267949 0 0" />
    <parent link="base_link" />
    <child link="right_leg" />
    <axis xyz="0 0 0" />
  </joint>
  <link name="sensor_box">
    <inertial>
      <origin xyz="-1.38777878078145E-16 0.0253479649063364 -1.40813899445239E-17" rpy="0 0 0" />
      <mass value="5.54829934163486" />
      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
    </inertial>
    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
  </link>
  <joint name="sensor_box_joint" type="fixed">
    <origin xyz="0.2027572 0 -0.177" rpy="1.5707963267949 0 0" />
    <parent link="base_link" />
    <child link="sensor_box" />
    <axis xyz="0 0 0" />
  </joint>
  <link name="base_footprint" />
  <joint name="base_footprint_joint" type="fixed">
    <origin xyz="-0.0222427999999998 0 -1.034" rpy="0 0 0" />
    <parent link="base_link" />
    <child link="base_footprint" />
    <axis xyz="0 0 0" />
  </joint>
  <link name="imu_link" />
  <joint name="imu_link_joint" type="fixed">
    <origin xyz="0.5277572 0 -0.0209520000000005" rpy="0 0 0" />
    <parent link="base_link" />
    <child link="imu_link" />
    <axis xyz="0 0 0" />
  </joint>
  <link name="gps_link" />
  <joint name="gps_link_joint" type="fixed">
    <origin xyz="0 0 0" rpy="0 0 0" />
    <parent link="base_link" />
    <child link="gps_link" />
    <axis xyz="0 0 0" />
  </joint>
  <link name="zed_center" />
  <joint name="zed_center_joint" type="fixed">
    <origin xyz="0.5037567 0 0.0152379999999996" rpy="0 0 0" />
    <parent link="base_link" />
    <child link="zed_center" />
    <axis xyz="0 0 0" />
  </joint>
  <link name="front_w_l">
    <inertial>
      <origin xyz="0.0169585900383 -6.75068276955737E-05 1.52646951752655E-05" rpy="0 0 0" />
      <mass value="0.630032967311711" />
      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
    </inertial>
    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
  </link>
  <joint name="front_wl_j" type="continuous">
    <origin xyz="0.45576 0.4305 -0.904" rpy="3.1416 0 1.5708" />
    <parent link="base_link" />
    <child link="front_w_l" />
    <axis xyz="1 0 0" />
  </joint>
  <link name="front_w_r">
    <inertial>
      <origin xyz="0.0169585900289108 -6.75068276941859E-05 1.52646951756819E-05" rpy="0 0 0" />
      <mass value="0.630032967311706" />
      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
    </inertial>
    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
  </link>
  <joint name="front_wr_j" type="continuous">
    <origin xyz="0.45576 -0.4305 -0.904" rpy="0 0 -1.5708" />
    <parent link="base_link" />
    <child link="front_w_r" />
    <axis xyz="-1 0 0" />
  </joint>
  <link name="back_c_l">
    <inertial>
      <origin xyz="0.0408020089137942 -2.20027751224317E-06 -0.0753064138736016" rpy="0 0 0" />
      <mass value="1.78018975141913" />
      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
    </inertial>
    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
  </link>
  <joint name="back_cl_j" type="continuous">
    <origin xyz="-0.53224 0.37 -0.74193" rpy="-3.1578E-16 2.3679E-16 -3.1416" />
    <parent link="base_link" />
    <child link="back_c_l" />
    <axis xyz="0 0 1" />
    <limit effort="10000" velocity="1000"/>
    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
  </joint>
  <link name="back_w_l">
    <inertial>
      <origin xyz="-0.000406180079597973 -6.75068276938251E-05 1.52646951747659E-05" rpy="0 0 0" />
      <mass value="0.630032967311717" />
      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
    </inertial>
    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
  </link>
  <joint name="back_wl_j" type="continuous">
    <origin xyz="0.079407 0 -0.15715" rpy="1.5708 -3.1578E-16 1.5708" />
    <parent link="back_c_l" />
    <child link="back_w_l" />
    <axis xyz="-1 0 0" />
  </joint>
  <link name="back_c_r">
    <inertial>
      <origin xyz="-0.0408020085623402 2.19978087612205E-06 -0.0753064146672595" rpy="0 0 0" />
      <mass value="1.78018973135585" />
      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
    </inertial>
    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
  </link>
  <joint name="back_cr_j" type="continuous">
    <origin xyz="-0.53224 -0.37 -0.74193" rpy="0 0 0" />
    <parent link="base_link" />
    <child link="back_c_r" />
    <axis xyz="0 0 1" />
    <limit effort="10000" velocity="1000"/>
    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
  </joint>
  <link name="back_w_r">
    <inertial>
      <origin xyz="-0.000406180073682316 -6.75068276933533E-05 1.52646951745439E-05" rpy="0 0 0" />
      <mass value="0.630032967311691" />
      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
    </inertial>
    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
  </link>
  <joint name="back_wr_j" type="continuous">
    <origin xyz="-0.079407 0 -0.15715" rpy="1.5708 0 -1.5708" />
    <parent link="back_c_r" />
    <child link="back_w_r" />
    <axis xyz="-1 0 0" />
  </joint>
  <link name="front_m_l">
    <inertial>
      <origin xyz="0.000172348602596462 0.00360003940885012 0.0476290867686325" rpy="0 0 0" />
      <mass value="0.0474773626136393" />
      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
    </inertial>
    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
  </link>
  <joint name="front_ml_j" type="fixed">
    <origin xyz="0.45576 0.30769 -0.904" rpy="-1.5708 -1.5272 0" />
    <parent link="base_link" />
    <child link="front_m_l" />
    <axis xyz="0 0 0" />
  </joint>
  <link name="front_m_r">
    <inertial>
      <origin xyz="0.0323709132313685 0.000104130448797535 1.52149314511518E-05" rpy="0 0 0" />
      <mass value="0.0474773626136397" />
      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
    </inertial>
    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
  </link>
  <joint name="front_mr_j" type="fixed">
    <origin xyz="0.45926 -0.38769 -0.904" rpy="3.1416 0 1.5708" />
    <parent link="base_link" />
    <child link="front_m_r" />
    <axis xyz="0 0 0" />
  </joint>

  <link name="camera_link">
    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

    <inertial>
      <mass value="1e-5" />
      <origin xyz="0 0 0" rpy="0 0 0"/>
      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
    </inertial>
  </link>
  <joint name="camera_joint" type="fixed">
    <axis xyz="0 1 0" />
    <origin xyz="0.5 0 0.055" rpy="0 -1 0"/>
    <parent link="base_link"/>
    <child link="camera_link"/>
  </joint>

</robot>

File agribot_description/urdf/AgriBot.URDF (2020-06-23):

<?xml version="1.0"?>

<robot name="AgriBot">
  <link name="base_link">
    <inertial>
      <origin xyz="0.0806751514089021 0.89713157182701 0.2395472804545" rpy="0 0 0" />
      <mass value="4.12089235661957" />
      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
    </inertial>
    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
  </link>
  <link name="left_leg">
    <inertial>
      <origin xyz="-0.00274695482569587 -0.104877884752421 0.160222376467588" rpy="0 0 0" />
      <mass value="2.68279427592666" />
      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
    </inertial>
    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
  </link>
  <joint name="left_leg_j" type="fixed">
    <origin xyz="0.41455 -0.038812 1.4369" rpy="1.5719 -1.0644E-15 -0.010452" />
    <parent link="base_link" />
    <child link="left_leg" />
    <axis xyz="0 0 0" />
  </joint>
  <link name="left_fron_motor">
    <inertial>
      <origin xyz="0.000943512691755855 0.0092550922633271 0.00230005668672162" rpy="0 0 0" />
      <mass value="0.0474773625746306" />
      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
    </inertial>
    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
  </link>
  <joint name="left_fron_motor_j" type="fixed">
    <origin xyz="-0.01698 0.36093 -0.26715" rpy="-1.5708 -6.1383E-08 -1.5708" />
    <parent link="left_leg" />
    <child link="left_fron_motor" />
    <axis xyz="0 0 1" />
  </joint>
  <link name="left_fron_wheel">
    <inertial>
      <origin xyz="0.0164626876197982 -6.48862040431297E-05 1.45754210374438E-05" rpy="0 0 0" />
      <mass value="0.655479868012591" />
      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
    </inertial>
    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
  </link>
  <joint name="left_fron_wheel_j" type="continuous">
    <origin xyz="0.0009283 0.005651 0.077486" rpy="-3.1405 -1.5708 3.1405" />
    <parent link="left_fron_motor" />
    <child link="left_fron_wheel" />
    <axis xyz="1 0 0" />
  </joint>
  <link name="left_back_u">
    <inertial>
      <origin xyz="-2.19978721283098E-06 0.0818439163469187 -0.0386054008005605" rpy="0 0 0" />
      <mass value="1.78018973150026" />
      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
    </inertial>
    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
  </link>
  <joint name="left_back_u_j" type="continuous">
    <origin xyz="0 0.37508 0.79461" rpy="6.1383E-08 6.599E-09 3.1416" />
    <parent link="left_leg" />
    <child link="left_back_u" />
    <axis xyz="0 -1 0" />
  </joint>
  <link name="left_back_wheel">
    <inertial>
      <origin xyz="0.0169585900650365 -6.75068281532631E-05 1.52646950466462E-05" rpy="0 0 0" />
      <mass value="0.630032967450187" />
      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
    </inertial>
    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
  </link>
  <joint name="left_back_wheel_j" type="revolute">
    <origin xyz="-0.017365 0 0" rpy="0 -1.7347E-18 0" />
    <parent link="left_back_u" />
    <child link="left_back_wheel" />
    <axis xyz="-1 0 0" />
    <limit effort="0" velocity="0" />
  </joint>
  <link name="right_leg">
    <inertial>
      <origin xyz="0.0227490125503702 0.456034950694976 0.508021591806585" rpy="0 0 0" />
      <mass value="2.68279427593309" />
      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
    </inertial>
    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
  </link>
  <joint name="right_leg_j" type="fixed">
    <origin xyz="-0.26178 0.31671 0.87731" rpy="1.5719 -1.0895E-15 -0.010452" />
    <parent link="base_link" />
    <child link="right_leg" />
    <axis xyz="0 0 0" />
  </joint>
  <link name="right_front_motor">
    <inertial>
      <origin xyz="0.000943512686206738 0.00925509225722426 0.00230005668662961" rpy="0 0 0" />
      <mass value="0.0474773625767179" />
      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
    </inertial>
    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
  </link>
  <joint name="right_front_motor_j" type="fixed">
    <origin xyz="0.036988 0.91907 0.080651" rpy="-1.5708 6.1383E-08 1.5708" />
    <parent link="right_leg" />
    <child link="right_front_motor" />
    <axis xyz="0 0 0" />
  </joint>
  <link name="right_front_wheel">
    <inertial>
      <origin xyz="0.0164626875242103 -6.48860876186208E-05 1.46720923717147E-05" rpy="0 0 0" />
      <mass value="0.655479867807164" />
      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
    </inertial>
    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
  </link>
  <joint name="right_front_wheel_j" type="continuous">
    <origin xyz="0.0009283 0.005651 0.077486" rpy="3.1416 -1.5708 0" />
    <parent link="right_front_motor" />
    <child link="right_front_wheel" />
    <axis xyz="1 0 0" />
  </joint>
  <link name="right_back_u">
    <inertial>
      <origin xyz="-2.2002845199709E-06 0.0818439155528921 -0.0386053996730705" rpy="0 0 0" />
      <mass value="1.78018971143072" />
      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
    </inertial>
    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
  </link>
  <joint name="right_back_u_j" type="continuous">
    <origin xyz="0.020005 0.93508 1.1424" rpy="6.1383E-08 6.599E-09 3.1416" />
    <parent link="right_leg" />
    <child link="right_back_u" />
    <axis xyz="0 -1 0" />
  </joint>
  <link name="right_back_wheel">
    <inertial>
      <origin xyz="0.0169585900420705 -6.75068281608127E-05 1.52646950382085E-05" rpy="0 0 0" />
      <mass value="0.630032967450165" />
      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
    </inertial>
    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
  </link>
  <joint name="right_back_wheel_j" type="continuous">
    <origin xyz="-0.017365 0 0" rpy="0 2.7756E-17 -1.6941E-21" />
    <parent link="right_back_u" />
    <child link="right_back_wheel" />
    <axis xyz="1 0 0" />
  </joint>

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

    <link name="front_bar_link" />

    <joint name="front_bar" type="fixed">
      <origin xyz="0.52 0 0" rpy="0 0 0" />
      <parent link="base_link" />
      <child link="front_bar_link" />
    </joint>

 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

    <link name="imu_link" />
    <joint name="imu" type="fixed">
      <origin xyz="-0.48 0.0 0.0" rpy="0 0 0" />
      <parent link="base_link" />
      <child link="imu_link" />
    </joint>

 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

    <link name="gps_frame_id" />
    <joint name="gps" type="fixed">
      <origin xyz="0.0 0.0 0.0" rpy="0 0 0" />
      <parent link="base_link" />
      <child link="gps_frame_id" />
    </joint>

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

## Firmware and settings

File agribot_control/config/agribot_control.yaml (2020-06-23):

agribot:
  # Publish all joint states -----------------------------------
  joint_state_controller:
    type: joint_state_controller/JointStateController
    publish_rate: 50  

  Diff_base_controller:
    type: "diff_drive_controller/DiffDriveController"
    left_wheel  : 'front_wl_j'
    right_wheel : 'front_wr_j'
#Velocity Controllers ---------------------------------------
  # left_front_joint:
  #   type: effort_controllers/JointVelocityController
  #   joint: front_wl_j
  #   pid: {p: 100.0, i: 10.0, d: 0.01}
  # right_front_joint:
  #   type: effort_controllers/JointVelocityController
  #   joint: front_wr_j
  #   pid: {p: 100.0, i: 10.0, d: 0.01}
#Position Controllers ---------------------------------------
  left_caster_joint:
    type: effort_controllers/JointPositionController
    joint: back_cl_j
    pid: {p: 80.0, i: 5.0, d: 0.00}
  right_caster_joint:
    type: effort_controllers/JointPositionController
    joint: back_cr_j
    pid: {p: 80.0, i: 5.0, d: 0.00}

    # pid: {p: 1.0, i: 0.01, d: 0.01}

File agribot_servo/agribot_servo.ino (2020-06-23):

/*%%%%%%%%%%%%%%%%%%%%%%%%%%%%%%%%%%%%%%%%%%%%%%%%%%%%%%%%%%%%%%%
% ROS-Embedded Controller - Servo Joint in Agribot Platfrom     %
% by: Alireza Ahmadi                                            %
% University of Bonn- MSc Robotics & Geodetic Engineering       %
% Alireza.Ahmadi@uni-bonn.de                                    %
% https://github.com/PRBonn                              %
%%%%%%%%%%%%%%%%%%%%%%%%%%%%%%%%%%%%%%%%%%%%%%%%%%%%%%%%%%%%%%%%*/
#include <ros.h>
#include <ros/time.h>
#include <std_msgs/Int16MultiArray.h>
#include <std_msgs/Empty.h>

bool ROS_en  = true;

ros::NodeHandle  nh;

float ranges[2];

const int led_pin = 13;
// These constants won't change. They're used to give names to the pins used:
const int analogIn_right = A1;  // Analog input pin that the potentiometer is attached to
const int analogIn_left = A0;  // Analog input pin that the potentiometer is attached to

const int PulOut_left = 5; 
const int DirOut_left = 10; 

const int PulOut_right = 6; 
const int DirOut_right = 11; 

const int ledPin =  LED_BUILTIN;// the number of the LED pin

const int power_en = 12;

int Coef = 110;

int sensorValue_left = 0;        // value read from the pot
int sensorValue_right = 0;        // value read from the pot

int outputValue_left = 0;        // value output to the PWM (analog out)
int outputValue_right = 0;        // value output to the PWM (analog out)

int center_left = 0;        // global center variable of left caster
int center_right = 0;       // global center variable of right caster 

int center_f_left = 512;        //512
int center_f_right = 495 ;       //495

int center_b_left = 510-102;        //495-102
int center_b_right = 495-102;       //495-102

int telorance = 1;
int i=0;

int PWM_value = 400;

int old_sensorValue_left = 0;
int old_sensorValue_right = 0;

bool b_right = false;
bool b_left = false;

float D2S = 51/90;

int goal_r = 0.0;
int goal_l = 0.0;

int goal_r_old = 0.0;
int goal_l_old = 0.0;

bool Servo_stop = true;

int max_step = 91;

bool set_Zero = false;

int old_ModeFlag = 0;

void messageCb( const std_msgs::Int16MultiArray& ServoPose){
  Toggle_led(-1,70);

  if(ServoPose.data[2] != old_ModeFlag){
    set_Zero = true;
    if(ServoPose.data[2] == 0){
      center_left = center_f_left;
      center_right = center_f_right;
    }else{
      center_left = center_b_left;
      center_right = center_b_right;
    }
    old_ModeFlag = ServoPose.data[2];
  }
  
  if(ServoPose.data[0] != 900){
    if(abs(ServoPose.data[0]) > max_step + telorance) ServoPose.data[0] = max_step*(ServoPose.data[0]/ServoPose.data[0]);
    goal_r = ((51*ServoPose.data[0])/90) + center_right;
    if(ServoPose.data[1] == 0)set_Zero = true;
    Servo_stop = false;
  }else{
    Servo_stop = true;
  }
  if(ServoPose.data[1] != 900){
    if(abs(ServoPose.data[1]) > max_step + telorance) ServoPose.data[1] = max_step*(ServoPose.data[1]/ServoPose.data[1]);
    goal_l = ((51*ServoPose.data[1])/90) + center_left;
    if(ServoPose.data[1] == 0)set_Zero = true;
    Servo_stop = false;
  }else{
    Servo_stop = true;
  }


//  if(ServoPose.data[0] != 900 && ServoPose.data[1] != 900){
//    if(ServoPose.data[0] == 0 || ServoPose.data[1] == 0 || ServoPose.data[2] != old_ModeFlag){
//      set_Zero = true;
//      if(ServoPose.data[2] == 0){
//        center_left = center_f_left;
//        center_right = center_f_right;
//      }else{
//        center_left = center_b_left;
//        center_right = center_b_right;
//      }
//      old_ModeFlag = ServoPose.data[2];
//    }
//  
//    if(abs(ServoPose.data[0]) > max_step + telorance) ServoPose.data[0] = max_step*(ServoPose.data[0]/ServoPose.data[0]);
//    goal_r = D2S * ServoPose.data[0] + center_right;
//
//    if(abs(ServoPose.data[1]) > max_step + telorance) ServoPose.data[1] = max_step*(ServoPose.data[1]/ServoPose.data[1]);
//    goal_l = D2S * ServoPose.data[1] + center_left;
//    
//    Servo_stop = false;
//  }else{
//    Servo_stop = true;
//  }
}

ros::Subscriber<std_msgs::Int16MultiArray> sub("ServoPose", messageCb );

void setup() {
  delay(100);
  if(!ROS_en){
    Toggle_led(2,150);
    // initialize serial communications at 9600 bps:
    Serial.begin(9600);
  }else{
    Toggle_led(3,150);
    nh.initNode();
    nh.subscribe(sub);
  }
  
  setPwmFrequency(5, (int)(62500/2));
  setPwmFrequency(6, (int)(62500/2));
  pinMode(DirOut_right, OUTPUT);
  pinMode(DirOut_left, OUTPUT);

  pinMode(led_pin,OUTPUT);
  
  pinMode(power_en, OUTPUT);
  digitalWrite(power_en, HIGH);
  
  pinMode(A2, OUTPUT);
  pinMode(A3, OUTPUT);
  digitalWrite(A2, HIGH);
  digitalWrite(A3, HIGH);

  delay(100);

// set Initial potision to 0 or 180
  center_left = center_f_left;
  center_right = center_f_right;
//  center_left = center_b_left;
//  center_right = center_b_right;

  int tmp_r = (51*0)/90;
  int tmp_l = (51*0)/90;
  while(!intial_position_both(center_right+tmp_r,center_left+tmp_l)){
    if(!ROS_en){
      print_val();
    }
  }
  for(int cnt=0; cnt<20; cnt++){
      set_position_both(center_right+tmp_r-3,center_left+tmp_r-3);
      delay(20);
      set_position_both(center_right+tmp_r+1,center_left+tmp_r+1);
      delay(20);
      set_position_both(center_right+tmp_r,center_left+tmp_r);
  }
  
  goal_r = center_right;
  goal_r_old = goal_r;

  goal_l = center_left;
  goal_l_old = goal_l;

}
void loop() {
  
  if(goal_r_old != goal_r || goal_l_old != goal_l){
    goal_r_old = goal_r;
    goal_l_old = goal_l;
    set_position_both(goal_r,goal_l);
    if(goal_r == center_right && goal_l == center_left){
      for(int cnt=0; cnt<30; cnt++){
        set_position_both(center_right,center_left);
        delay(20);
      }
    }
  }

  if(set_Zero){
    while(!intial_position_both(center_right,center_left)){
      delay(1);
    }
    set_Zero = false;
  }
  
  Stop_both(goal_r,goal_l);
  if(!ROS_en){
    print_val();
  }else{
    nh.spinOnce();
  }
  delay(5);
}

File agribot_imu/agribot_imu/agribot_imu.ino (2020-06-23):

/*%%%%%%%%%%%%%%%%%%%%%%%%%%%%%%%%%%%%%%%%%%%%%%%%%%%%%%%%%%
% ROSSerial Node-IMU BNO055 Bosch sensor(Leonardo-arduino) %
% by: Alireza Ahmadi                                       %
% University of Bonn- MSc Robotics & Geodetic Engineering  %
% Alireza.Ahmadi@uni-bonn.de                               %
% https://github.com/PRBonn                         %
%%%%%%%%%%%%%%%%%%%%%%%%%%%%%%%%%%%%%%%%%%%%%%%%%%%%%%%%%%*/

#define USE_USBCON //use this line just incase of using Arduino-Leonardo
#include <ros.h>
#include <sensor_msgs/Imu.h>
#include <Wire.h>
#include <Adafruit_Sensor.h>
#include <Adafruit_BNO055.h>
#include <utility/imumaths.h>

ros::NodeHandle  nh;
sensor_msgs::Imu imu_msg;
ros::Publisher pub("imu", &imu_msg);
char frame_id[] = "imu";

#define BNO055_SAMPLERATE_DELAY_MS (100)

Adafruit_BNO055 bno = Adafruit_BNO055(55);

void setup(){ 

  nh.initNode();
  nh.advertise(pub);

  /* Initialise the sensor */
  if(!bno.begin())
  {
    /* There was a problem detecting the BNO055 ... check your connections */
    Serial.print("Ooops, no BNO055 detected ... Check your wiring or I2C ADDR!");
    while(1);
  }

  delay(1000);

  bno.setExtCrystalUse(true);

  imu_msg.header.seq = 0;
  imu_msg.header.stamp = nh.now();
  imu_msg.header.frame_id = frame_id;


  imu_msg.orientation.x = 0;
  imu_msg.orientation.y = 0;
  imu_msg.orientation.z = 0;
  imu_msg.orientation.w = 0;

  imu_msg.orientation_covariance[0] = 0;
  imu_msg.orientation_covariance[1] = 0;
  imu_msg.orientation_covariance[2] = 0;

  imu_msg.orientation_covariance[3] = 0;
  imu_msg.orientation_covariance[4] = 0;
  imu_msg.orientation_covariance[5] = 0;

  imu_msg.orientation_covariance[6] = 0;
  imu_msg.orientation_covariance[7] = 0;
  imu_msg.orientation_covariance[8] = 0;


  imu_msg.angular_velocity.x = 0;
  imu_msg.angular_velocity.y = 0;
  imu_msg.angular_velocity.z = 0;

  imu_msg.angular_velocity_covariance[0] = 0;
  imu_msg.angular_velocity_covariance[1] = 0;
  imu_msg.angular_velocity_covariance[2] = 0;

  imu_msg.angular_velocity_covariance[3] = 0;
  imu_msg.angular_velocity_covariance[4] = 0;
  imu_msg.angular_velocity_covariance[5] = 0;

  imu_msg.angular_velocity_covariance[6] = 0;
  imu_msg.angular_velocity_covariance[7] = 0;
  imu_msg.angular_velocity_covariance[8] = 0;


  imu_msg.linear_acceleration.x = 0;
  imu_msg.linear_acceleration.y = 0;
  imu_msg.linear_acceleration.z = 0;

  imu_msg.linear_acceleration_covariance[0] = 0;
  imu_msg.linear_acceleration_covariance[1] = 0;
  imu_msg.linear_acceleration_covariance[2] = 0;

  imu_msg.linear_acceleration_covariance[3] = 0;
  imu_msg.linear_acceleration_covariance[4] = 0;
  imu_msg.linear_acceleration_covariance[5] = 0;

  imu_msg.linear_acceleration_covariance[6] = 0;
  imu_msg.linear_acceleration_covariance[7] = 0;
  imu_msg.linear_acceleration_covariance[8] = 0;
}

void loop(){
  /* Get a new sensor event */
  sensors_event_t event;

  // Possible vector values can be:
  // - VECTOR_ACCELEROMETER - m/s^2
  // - VECTOR_MAGNETOMETER  - uT
  // - VECTOR_GYROSCOPE     - rad/s
  // - VECTOR_EULER         - degrees
  // - VECTOR_LINEARACCEL   - m/s^2
  // - VECTOR_GRAVITY       - m/s^2
  imu::Vector<3> Lin_acc = bno.getVector(Adafruit_BNO055::VECTOR_LINEARACCEL);
  imu::Vector<3> gyro_raw = bno.getVector(Adafruit_BNO055::VECTOR_GYROSCOPE);

   
  bno.getEvent(&event);
  
  imu_msg.header.seq++;
  imu_msg.header.stamp = nh.now();

  // Doesn't work:
  pub.publish(&imu_msg);

  imu_msg.orientation.x = event.orientation.z;
  imu_msg.orientation.y = event.orientation.y;
  imu_msg.orientation.z = event.orientation.x;

//  imu_msg.orientation_covariance[0] = 0.01;
//  imu_msg.orientation_covariance[1] = 0;
//  imu_msg.orientation_covariance[2] = 0;
//
//  imu_msg.orientation_covariance[3] = 0;
//  imu_msg.orientation_covariance[4] = 0.01;
//  imu_msg.orientation_covariance[5] = 0;
//
//  imu_msg.orientation_covariance[6] = 0;
//  imu_msg.orientation_covariance[7] = 0;
//  imu_msg.orientation_covariance[8] = 0.01;

  imu_msg.angular_velocity.x = gyro_raw.x();
  imu_msg.angular_velocity.y = gyro_raw.y();
  imu_msg.angular_velocity.z = gyro_raw.z();

//  imu_msg.angular_velocity_covariance[0] = 0.01;
//  imu_msg.angular_velocity_covariance[1] = 0;
//  imu_msg.angular_velocity_covariance[2] = 0;
//
//  imu_msg.angular_velocity_covariance[3] = 0;
//  imu_msg.angular_velocity_covariance[4] = 0.01;
//  imu_msg.angular_velocity_covariance[5] = 0;
//
//  imu_msg.angular_velocity_covariance[6] = 0;
//  imu_msg.angular_velocity_covariance[7] = 0;
//  imu_msg.angular_velocity_covariance[8] = 0.01;

  imu_msg.linear_acceleration.x = Lin_acc.x();
  imu_msg.linear_acceleration.y = Lin_acc.y();
  imu_msg.linear_acceleration.z = Lin_acc.z();
  
//  imu_msg.linear_acceleration_covariance[0] = 0.01;
//  imu_msg.linear_acceleration_covariance[1] = 0;
//  imu_msg.linear_acceleration_covariance[2] = 0;
//
//  imu_msg.linear_acceleration_covariance[3] = 0;
//  imu_msg.linear_acceleration_covariance[4] = 0.01;
//  imu_msg.linear_acceleration_covariance[5] = 0;
//
//  imu_msg.linear_acceleration_covariance[6] = 0;
//  imu_msg.linear_acceleration_covariance[7] = 0;
//  imu_msg.linear_acceleration_covariance[8] = 0.01;

  nh.spinOnce();
  delay(BNO055_SAMPLERATE_DELAY_MS);
}

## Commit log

2020-07-03 Agribot_gazebo plant models updated
    [big_plant.stl, model.sdf, small_plant.stl]
2021-02-10 navigation and local planer add
    [AgribotLocalPlanner.cfg]
